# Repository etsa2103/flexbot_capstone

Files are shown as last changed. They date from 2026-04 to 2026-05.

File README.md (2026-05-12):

# FlexBot Reverse Engineering and ROS Integration

## Overview

The goal of this capstone project was to repurpose the FlexBot so that it can serve as a general mobile platform for future robotics research and teaching projects at Penn. The FlexBot is a differential drive industrial robot donated to GRASP by Berkshire Grey.  

The repurposing process included documenting the robot’s hardware and electrical architecture, evaluating its custom control software, removing application-specific hardware, and integrating new systems including a LiDAR, external computer, and odometry pipeline. The completed system was integrated into ROS 2 to support teleoperation, odometry, and SLAM while also producing documentation for future users and development.

<p align="center">
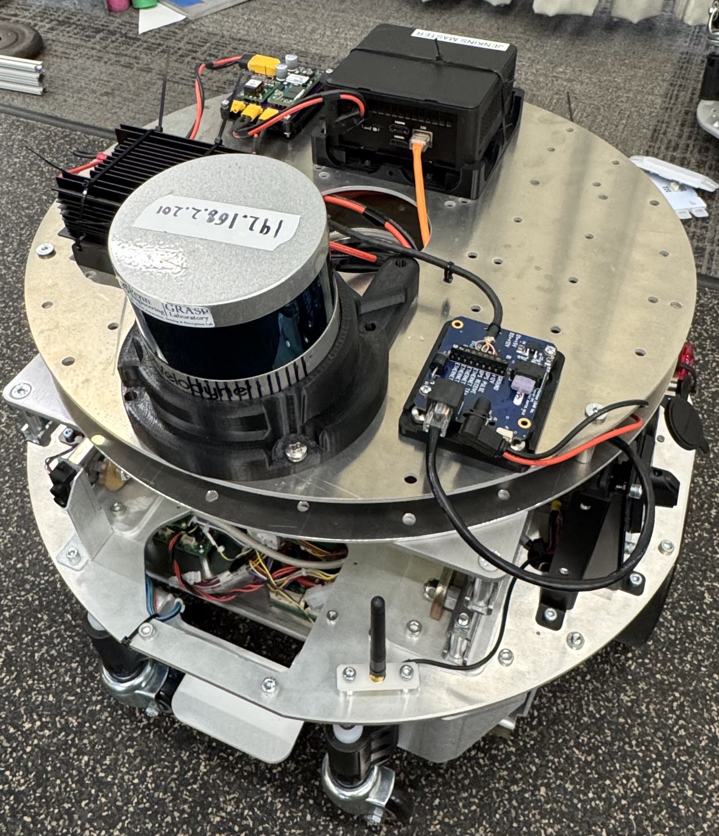
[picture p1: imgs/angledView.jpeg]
  
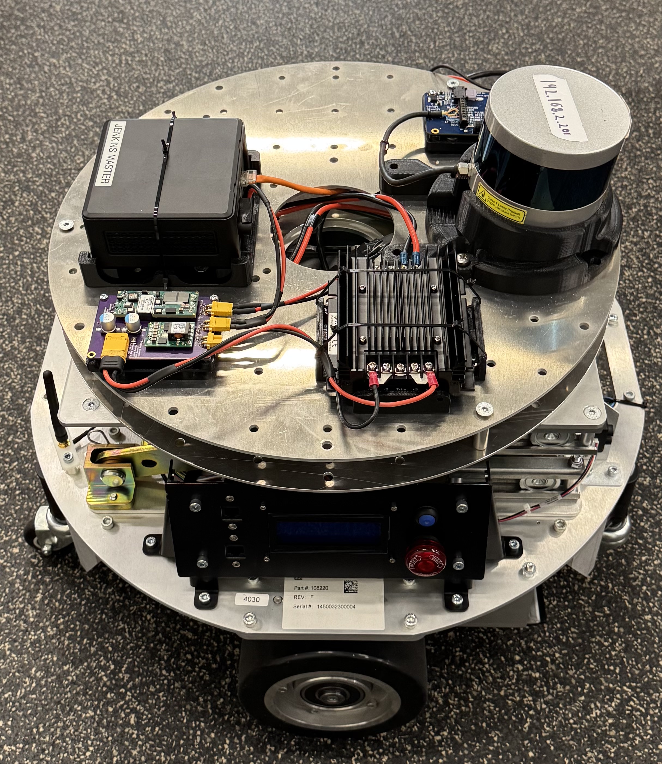
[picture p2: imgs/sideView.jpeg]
  
</p>

---

## Hardware

The robot hardware can be separated into three main components: the Mobile Base, the Scissor Lift Stage, and the Rotary Stage. Below is a brief description of each subsystem, while the full hardware documentation can be found on this [Miro Board](https://miro.com/app/board/uXjVJ2xI5w8=/).

### Mobile Base

The mobile base is the primary working platform of the robot and contains most of the core systems. Two drive motors provide mobility, while the onboard electronics manage power distribution, sensing, and computation. The base includes components such as the Motor Control Boards (MCBs), Power Distribution Board (PDB), sensors, LEDs, WiFi antennas, and the Application Processor Board (APB). These systems work together to support autonomous operation, sensor processing, and communication with external systems.

### Scissor Lift Stage

The scissor lift stage sits above the mobile base and provides vertical movement through a motorized scissor lift mechanism. It also contains a cable routing channel that allows wiring to safely pass from the mobile base to the upper stage without becoming pinched during movement.

### Rotary Stage

The rotary stage was originally designed to allow the top section of the robot to rotate independently from the base using a dedicated rotary motor and platform assembly. This stage remains present on the original FlexBots donated to Penn, but for this project it was removed and the available power was redirected to support the external computer and LiDAR.

---

## Electrical Connections

The diagram below shows the overall electrical layout of the robot and the connections between the major PCBs and subsystems. Rather than labeling every individual wire within each cable, the diagram focuses on the primary connectors and subsystem relationships to provide a clearer system-level overview.

<p align="center">
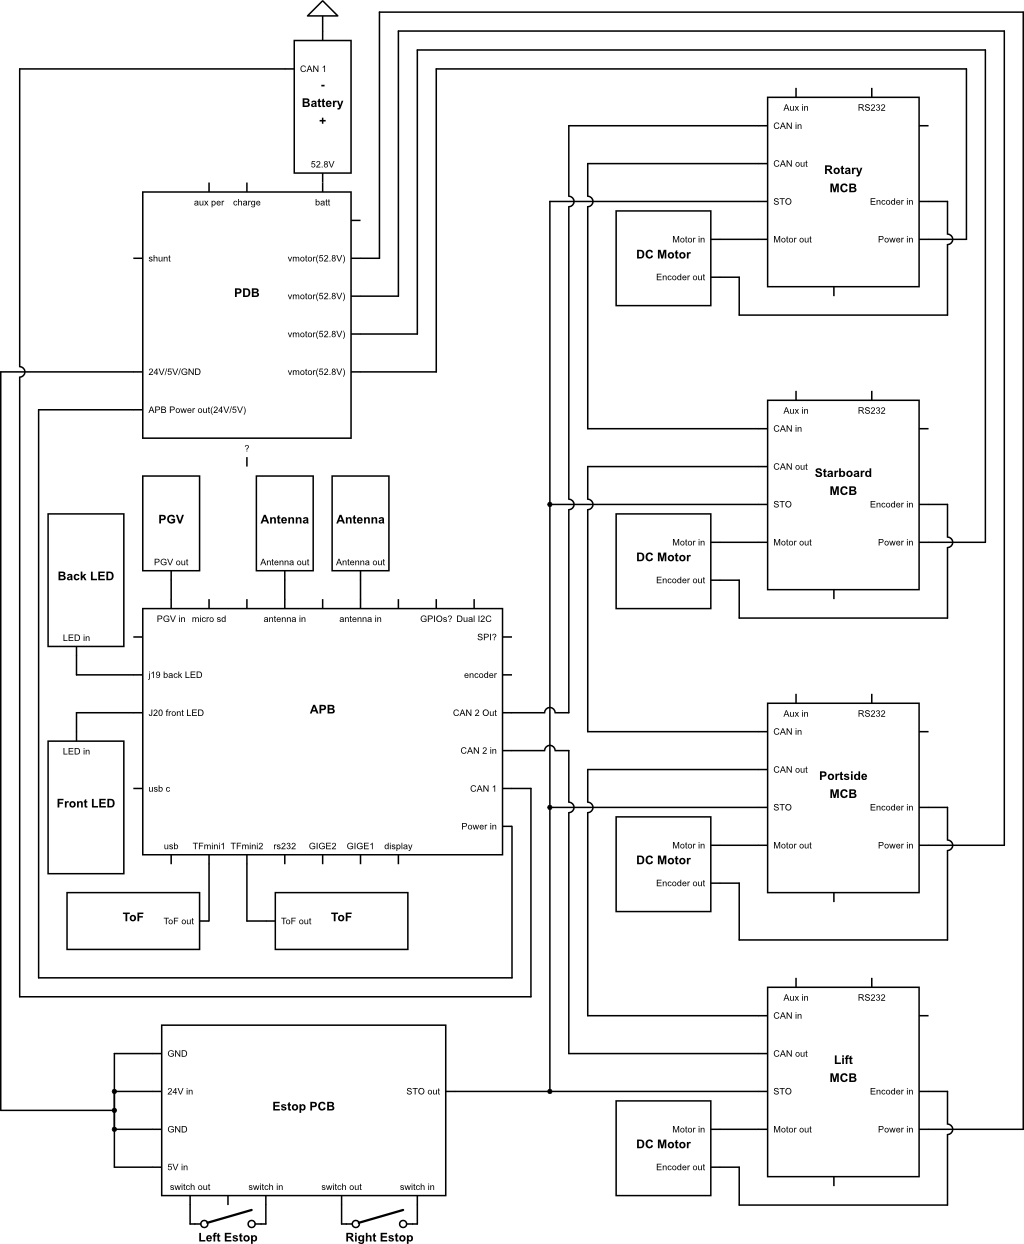
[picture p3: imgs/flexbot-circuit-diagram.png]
  
  <br>
  <font size="5"><b>Figure 1: Circuit Diagram of FlexBot Internal Electronics</b></font>
</p>

---

## Software Analysis

To gain control of the FlexBot’s internal systems, I first established direct serial communication with the onboard CPU. This allowed me to monitor the boot sequence and better understand the robot’s operating system environment. The CPU automatically attempted to connect to a WiFi network called `bg-flexbot-wifi6`, so I recreated the expected network environment in order to gain SSH access to the internal filesystem.

Reverse engineering the robot’s CAN network was necessary to gain control of the motors. With the help of Kartik Virmani from MOD Lab, CAN traffic was monitored while the robot’s built-in maintenance software executed known movement commands. By correlating CAN packets with specific robot actions, we identified the CAN IDs responsible for motor velocity commands and sensor data, ultimately allowing custom control scripts to bypass the original software stack.

All code developed for the low-level onboard computer can be found in [this branch](https://github.com/etsa2103/flexbot_capstone/tree/low_level_cpu) of the project repository. That branch also includes setup instructions and documentation for replicating the process.

---

## Modifications

Several hardware modifications were made to adapt the FlexBot for research applications and external hardware integration.

To bypass restrictions imposed by the proprietary safety board, the board was disconnected and 24V power was manually rerouted to the Safety Torque Off (STO) pins on the Motor Control Boards (MCBs). This 24V supply was sourced from the Power Distribution Board (PDB) and routed through both Emergency Stop (E-stop) buttons to preserve a functional hardware safety mechanism during operation.

In collaboration with Jaime Romero, the original rotary stage was removed and replaced with a custom top plate that provides a stable mounting surface for additional hardware. Custom 3D-printed mounts were also designed for the VLP-16 LiDAR, external high-level computer, and power distribution hardware. The CAD files for these mounts can be found [here](CAD). Power for the new hardware was sourced directly from the robot’s PDB and routed to the modified top assembly.

The resulting hardware architecture is shown below, while additional documentation can be found in the modified hardware section of the [Miro Board](https://miro.com/app/board/uXjVJ2xI5w8=/).

<p align="center">
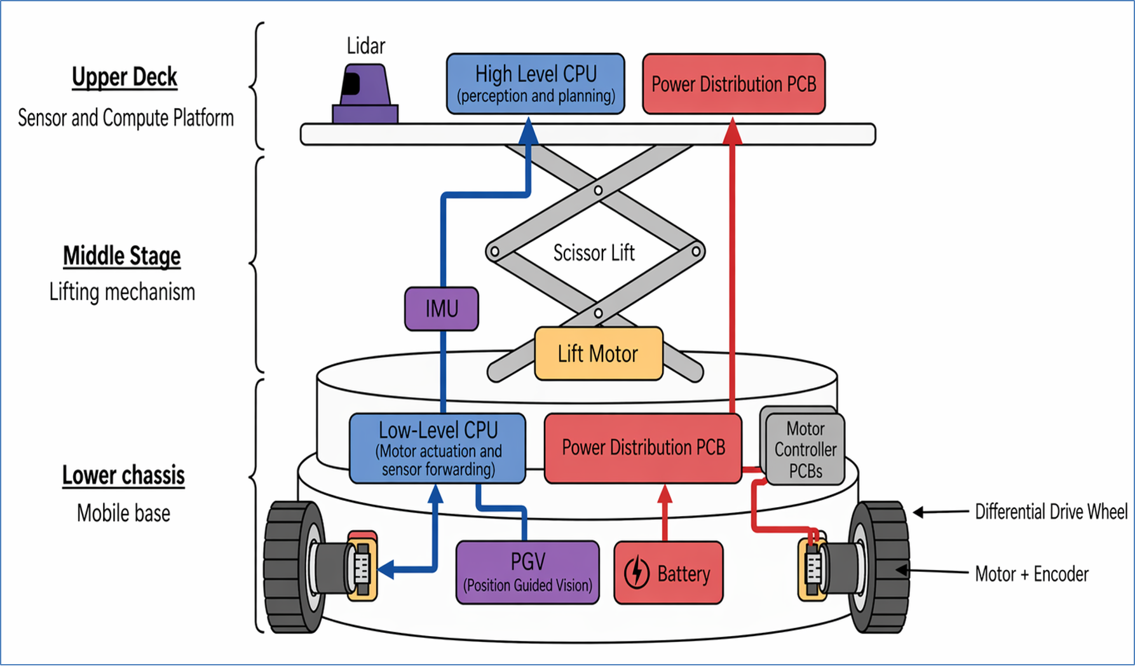
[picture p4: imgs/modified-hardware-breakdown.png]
  
  <br>
  <font size="5"><b>Figure 2: Hardware Breakdown of Modified FlexBot</b></font>
</p>

Because the original system relied on proprietary Berkshire Grey charging docks that were unavailable, an external charger was used to safely recharge the batteries.

---

## ROS Integration

To integrate the FlexBot into ROS 2, a dedicated Ethernet connection was established between the robot’s low-level embedded computer and the new external high-level computer. The low-level system processes raw hardware telemetry and continuously streams this data as UDP packets to the high-level computer. Custom ROS 2 nodes running on the high-level system capture the UDP data and publish it to standard ROS topics.

This architecture supports teleoperation, wheel odometry, and 2D SLAM using the integrated VLP-16 LiDAR. The overall software structure is summarized in the figure below.

<p align="center">
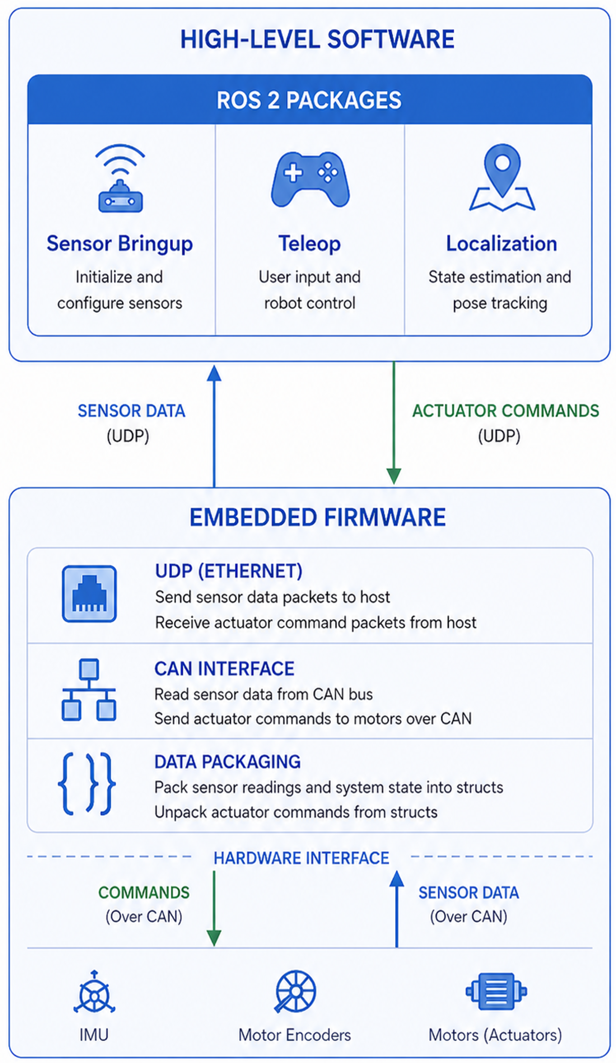
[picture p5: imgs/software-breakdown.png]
  
  <br>
  <font size="5"><b>Figure 3: Software Breakdown of Modified FlexBot</b></font>
</p>

Operational data, including maps, sensor feeds, and hardware telemetry, is visualized through a custom Foxglove Studio dashboard shown below.

<p align="center">
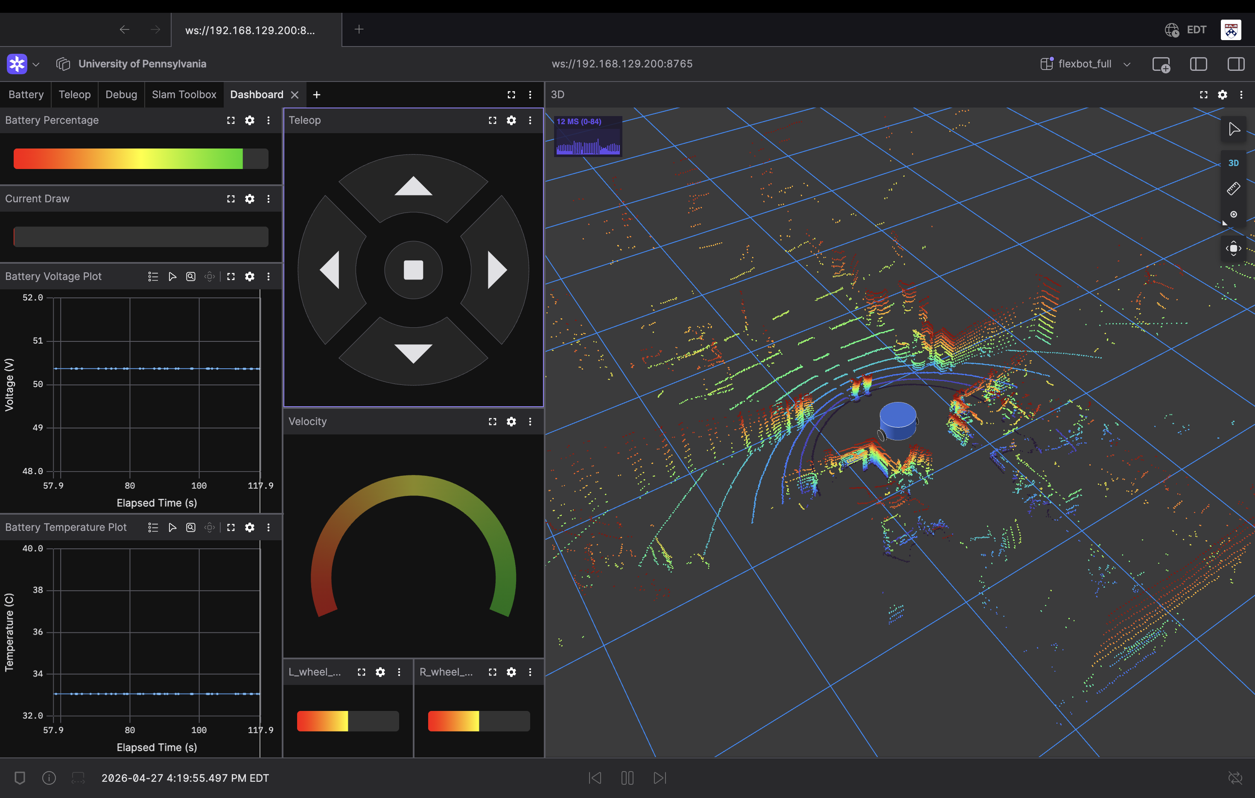
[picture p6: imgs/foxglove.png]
  
  <br>
  <font size="5"><b>Figure 4: Foxglove Visualizer</b></font>
</p>

All code developed for the high-level computer can be found in [this branch](https://github.com/etsa2103/flexbot_capstone/tree/high_level_cpu) of the repository. That branch also contains setup instructions and documentation for replicating the system.

---

## Side Notes and Next Steps

There are several remaining limitations and opportunities for future improvements to the FlexBot platform. When charging the robot, the main power switch must remain on or the batteries will not charge properly.

While the mobile base and LiDAR systems are fully operational, the scissor lift stage, LEDs, LCD display, PGV, and time-of-flight sensors are not yet fully integrated into ROS. The `low_level_cpu` branch contains several scripts that attempt to access these systems, but they are not currently exposed through ROS nodes running on the high-level computer.

Future development goals include integrating a 3D SLAM pipeline to better utilize the VLP-16 LiDAR, followed by obstacle avoidance and autonomous exploration or mapping behaviors for more advanced autonomous operation. Additional documentation collected throughout the project can be found in [this folder](additional_docs) of the repository.

---

## Acknowledgment

**Advisors:** I would like to thank Fernando Cladera and Dr. M. Ani Hsieh for their consistent advice and support throughout this project.

**Technical Contributors:** I would like to recognize Jaime Romero for his CAD designs and debugging assistance throughout the project. I would also like to recognize Kartik Virmani for his contributions to the reverse engineering and software development work included in this repository.

**Institutional Support:** Special thanks to Berkshire Grey for donating 30 FlexBot platforms to GRASP for research and educational use.

**Cornell University:** Thanks to Chris Bauer for providing documentation and insights from previous work on the robot platform.

## Appendix

- Kartik’s Github  
  https://github.com/virmani11kartik/bg_bot

- Kumar Robotics Github  
  https://github.com/KumarRobotics/kr_flexbot

- Miro Hardware Documentation  
  https://miro.com/app/board/uXjVJ2xI5w8=/

- Circuit diagram  
  https://www.circuitlab.com/circuit/pdmw4kpy644g/flexbot-circuit-diagram/

- Slack  
  https://app.slack.com/client/T09S1APBSHY/D09S4T6TL04

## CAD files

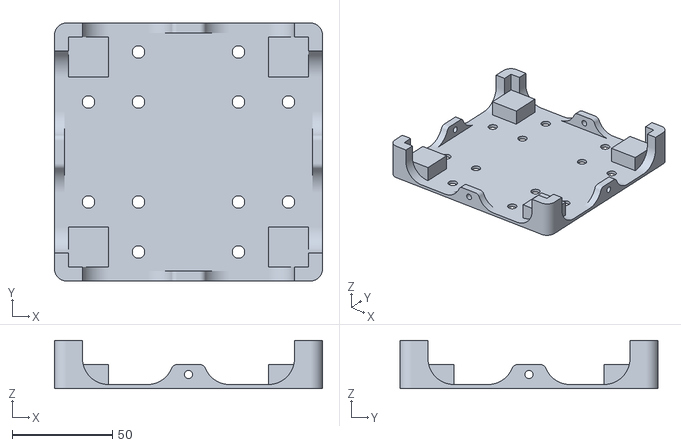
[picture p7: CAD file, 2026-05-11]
CAD/computer_mount.stl
134.0 x 129.0 x 24.0

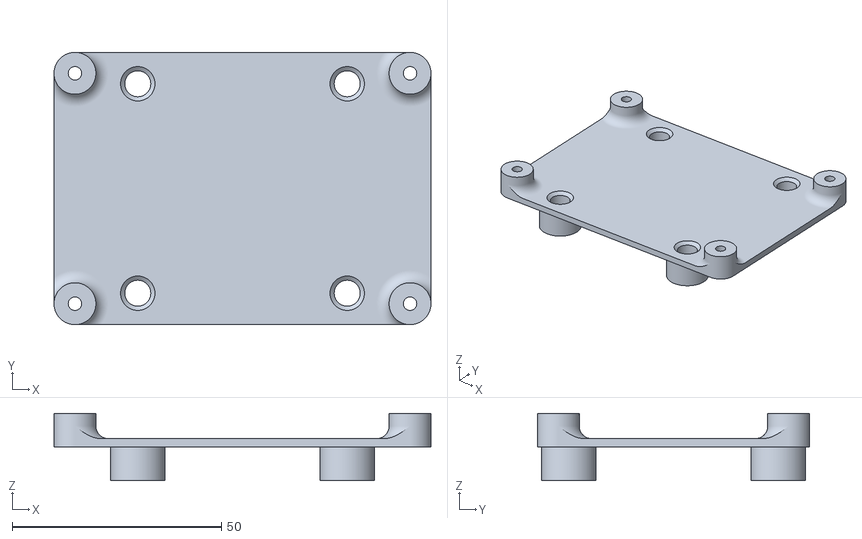
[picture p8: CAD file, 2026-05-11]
CAD/voltage_converter_stand.stl
90.0 x 65.0 x 16.0

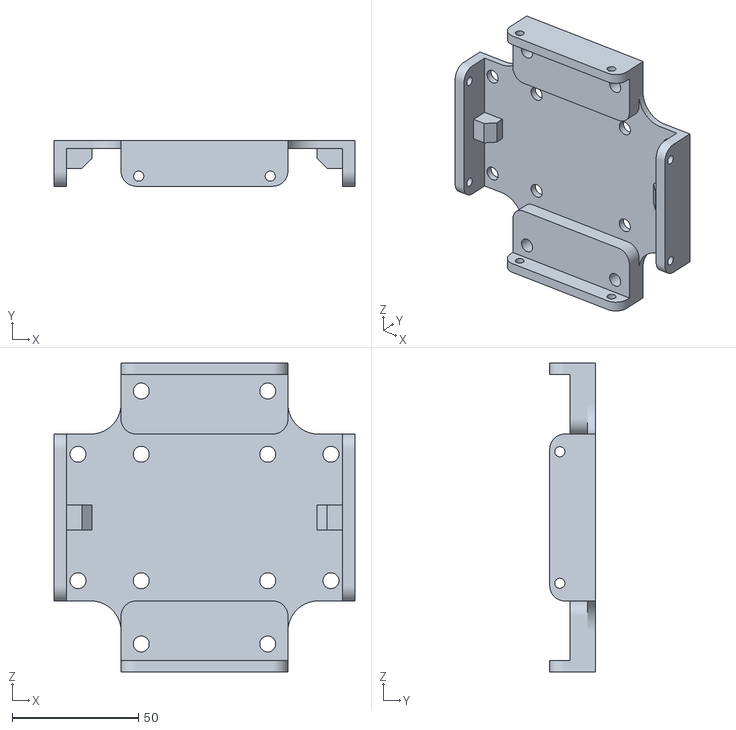
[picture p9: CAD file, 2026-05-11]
CAD/voltage_regulator_stand.stl
119.0 x 18.0 x 122.0

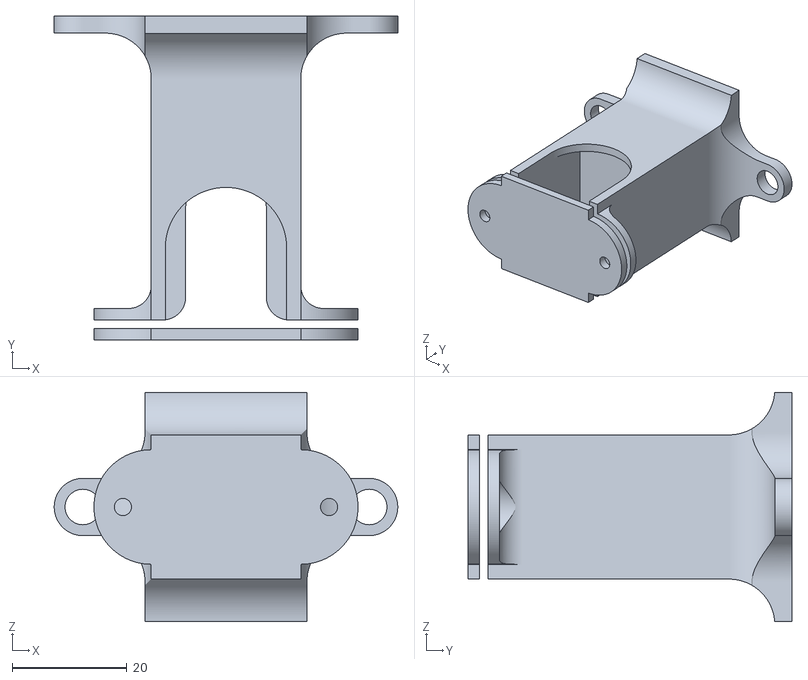
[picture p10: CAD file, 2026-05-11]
CAD/flir_camera_stand.stl
60.0 x 56.6 x 40.0

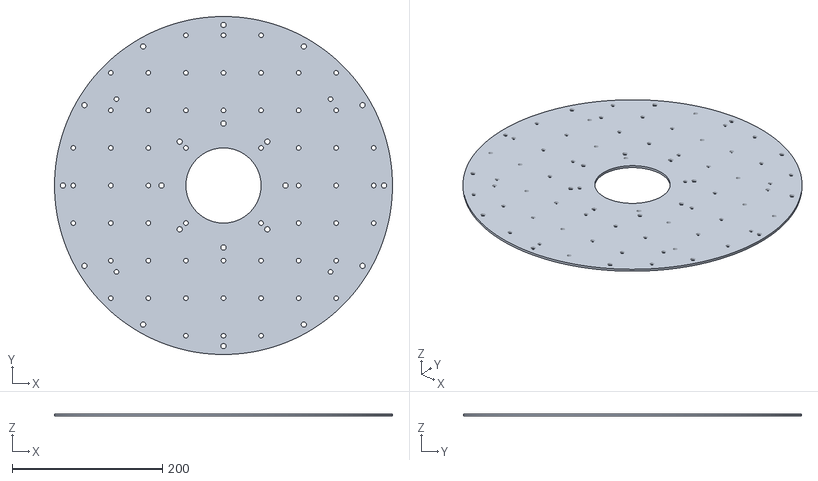
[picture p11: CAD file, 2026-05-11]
CAD/top_plate.stl
450.0 x 450.0 x 3.00

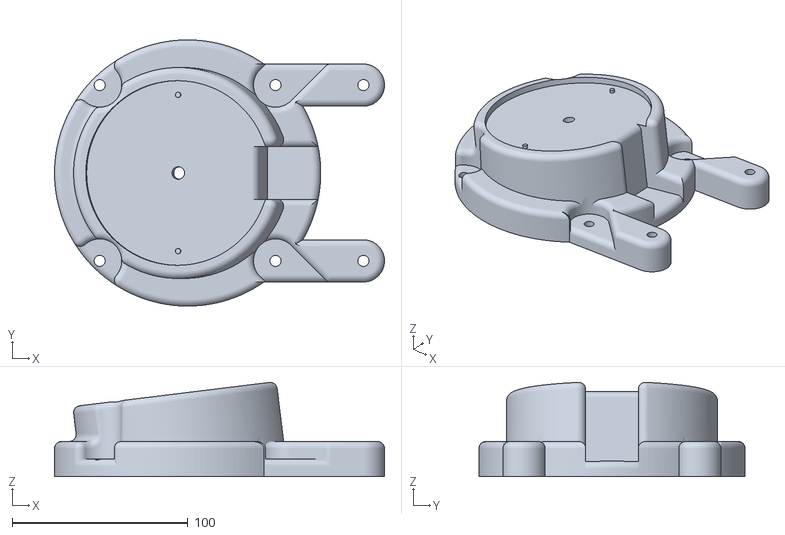
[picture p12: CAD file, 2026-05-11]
CAD/VLP16_mount.stl
187.7 x 151.5 x 53.6

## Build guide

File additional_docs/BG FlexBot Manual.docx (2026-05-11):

FlexBot Manual

FlexBot Theory of Operation Document Revision History

Revision | Date | Brief description of the Changes | Section(s) affected | Originator of Change
01 | 04/22/2022 | Initial Release | | Paul Conroy

The information in this document is current as the of the date of publication and is subject to change without notice.

Table of Contents

# Table of Figures

# FlexBot Overview

The FlexBot (PN: 108220) is the mobile robot that is a major component of the FlexTiles system. It is responsible for the movement and physical sortation of containers. It picks up containers from the induct FlexFeed, drives the container to the FlexShelves for temporary storage, and then drives it to the discharge FlexFeed. The FlexBot is capable of forward, limited backward, and rotation motion while the payload deck is capable of lift, lower, and rotation. Additionally, the FlexBot also has additional built in safety features to ensure safe operations.

The FlexBot has a fixed orientation described as port and starboard; standardizing orientation terminology to reduce chances of confusion. The port side of the FlexBot has the power switch while the starboard side of the FlexBot has the LCD. See below for pictures of the port and starboard sides of the FlexBot.

In this chapter, the part number for the illustrated item is displayed within the parentheses as shown in Figure 1.

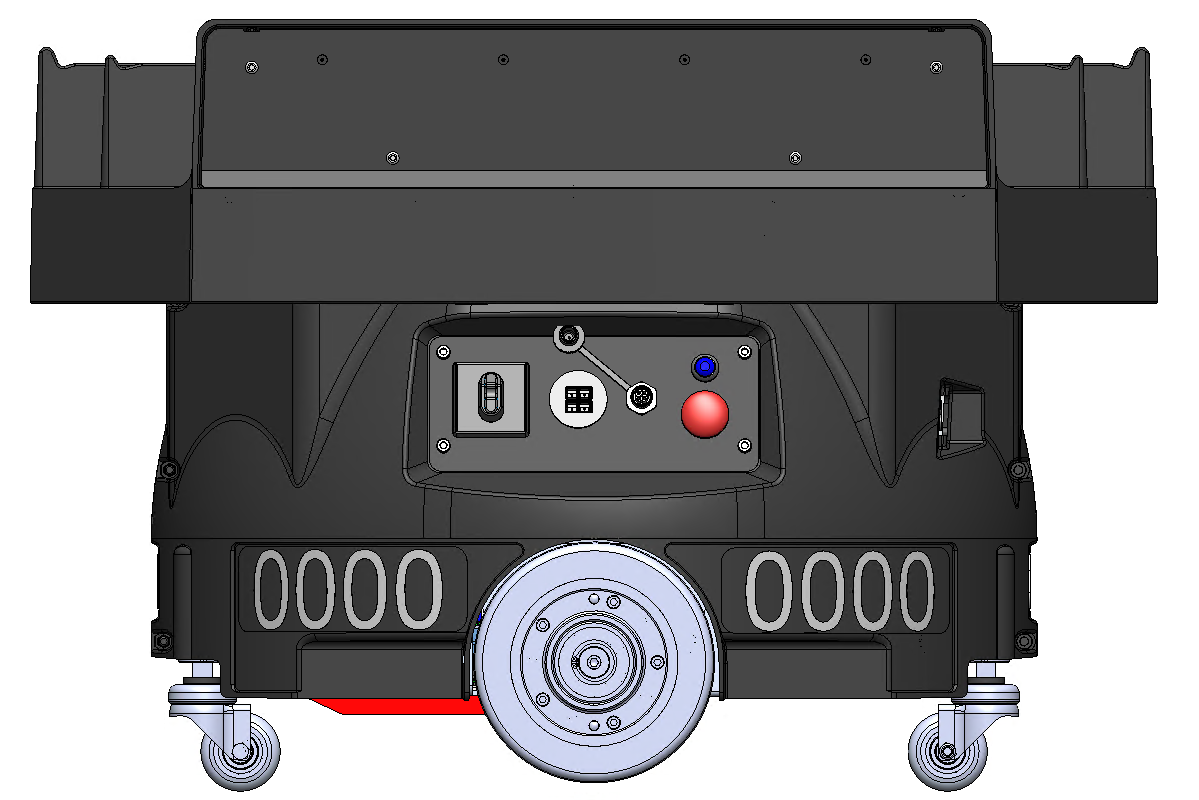
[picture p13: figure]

Figure 1 - Port Side of FlexBot

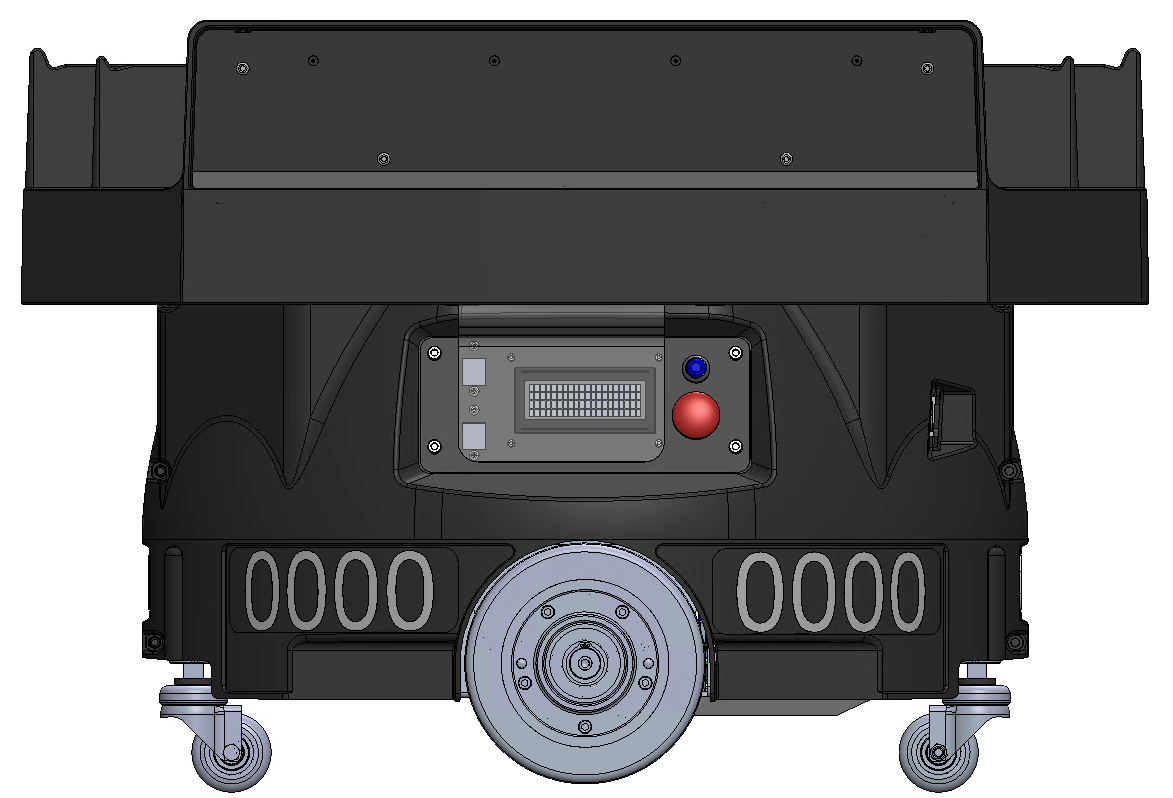
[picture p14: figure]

Figure 2 - Starboard Side of FlexBot

# Major Sections of the FlexBot

Section | Contains
Mobile Base | Contains the drive wheels and motors, the battery, the majority of the PCBAs
Payload Lift and Lower | Lifts and lowers the payload deck. It connects the drive base to the rotary stage.
Rotary Stage | Rotates the payload deck.
Payload Deck | The large plastic piece on top of the FlexBot that holds the containers as they move. There are four pairs of sensors used to detect whether there is a container on the payload deck.
FlexBot Housings and Covers | The outer pieces of plastic that cover the FlexBot.

## Mobile Base

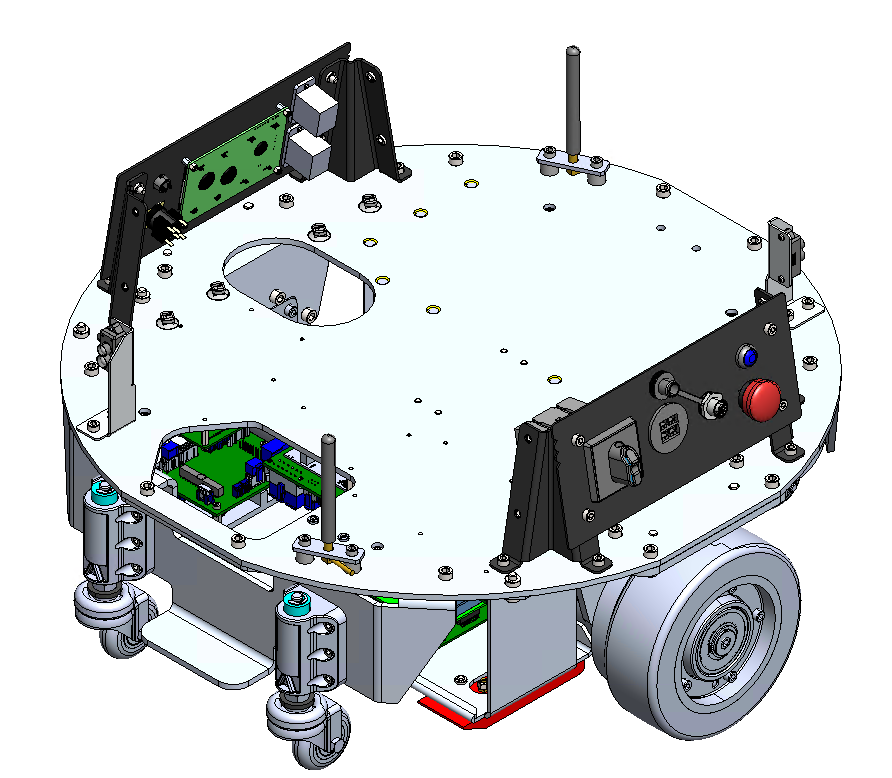
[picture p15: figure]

Figure 3 - Mobile Base: PN

The mobile base (PN: 107744) of the FlexBot is the core of the robot. It holds a large majority of components that are critical to the FlexBot’s function. Critical areas of the mobile base are listed below.

### Drive Motors

The drive motors (PN: 108471) are what allows the FlexBot to move in any direction. These motors can spin in both directions. FlexBots normal travel motions are forward and rotating either to the port or starboard. The port and starboard drive motors use the same part number.

Figure 4 - Drive Motors

### Battery

The FlexBot is powered by an onboard battery (PN: 109100). It requires periodic charging done automatically during normal operation and is managed by the FlexBot firmware. During maintenance and debugging the battery may have to be charged manually.

To access the battery you must remove, or swing open the caster bracket (PN: 108078) and then undo a Velcro strap that is holding the battery in place. Once the Velcro straps are undone, the battery can be partially slid out of the battery bay. Two final wired connections must be disconnected to free the battery from the FlexBot.

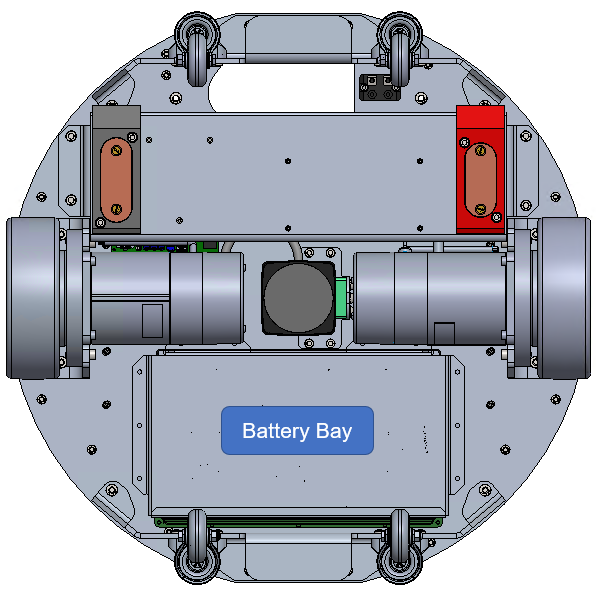
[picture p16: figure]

Figure 5 - Battery Bay Location

Figure 6 - Caster Bracket Location

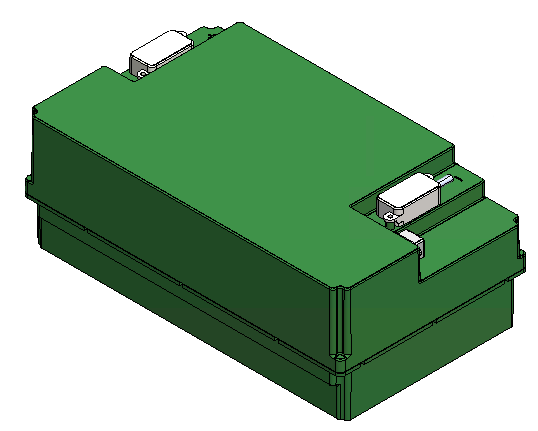
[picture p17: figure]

Figure 7 - Battery

### Battery Charging

The Charging & Electronics Bay ((PN: 109445) and contacts contain the electronic systems and pads for the FlexBot to charge the onboard battery using the charging points on the FlexTiles floor.

To reduce the risk of the charging system shorting, the negative contact is larger to ensure it connects first.

The positive charging contact block is colored red while the negative charging contact block is colored black.

Figure 8 - Charging and Electronics Bay

## User Interface (UI)

### Port Side UI

Figure 9 - Port Side

Part | Purpose
Power Switch | Physically controls the power state of the FlexBot. The power switch in the vertical position is off and in the horizontal position is on.
Emergency Stop | This red button inhibits any FlexBot motion when pressed. Rotate the button ¼ turn clockwise to release the button. There is an E-Stop button on both sides of the FlexBot. Both operate in the same manner. Only one needs to be engaged to stop motion. This button will blink twice per second when engaged and no light will be on in normal operation.
Dongle Port | The maintenance dongle plugs in this port when performing maintenance and debugging on the FlexBot
Shore power Port | Used to charge the battery manually when the FlexBot is off the field during maintenance.
Safety Reset Button | This blue button is used to reset the safety system in the FlexBot. There is one on both sides of the FlexBot. The small LED in the center of this button will signify one of the three different states: - Off- Normal Operation - Blinking twice per second - The button needs to be pressed to enter a normal operating state - Blinking once every three seconds - The FlexBot is located outside of the normal operating zone.

### Starboard Side UI

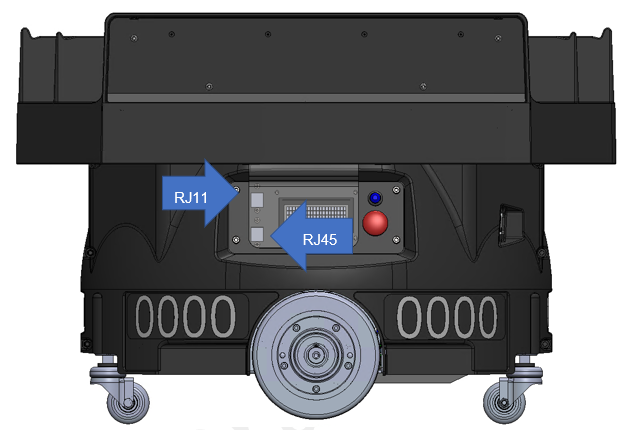
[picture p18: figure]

Figure 10 - Starboard Side

Part | Purpose
LCD Screen | Displays messages about errors, state of the FlexBot, FlexBot IP address, and other aspects of the FlexBot. The LCD will display relevant messages during maintenance steps.
Emergency Stop | This red button inhibits any FlexBot motion when pressed. Rotate the button ¼ turn clockwise to release the button. There is an E-Stop button on both sides of the FlexBot. Both operate in the same manner. Only one needs to be engaged to stop motion.
RJ11 Port | This port is used during the manufacturing process and is not active once it leaves the manufacturer.
RJ45 Port | Wired communication port used for direct Ethernet connection to the FlexBot.
Safety Reset Button | This blue button is used to reset the safety system in the FlexBot. There is one on both sides of the FlexBot. The small LED in the center of this button will signify one of the three different states: - Off- Normal Operation - Blinking twice per second - The button needs to be pressed to enter a normal operating state - Blinking once every three seconds - The FlexBot is located outside of the normal operating zone.

## Casters

The four casters (PN: 114307), two on the front and two on the rear, provide independent suspension for the FlexBot.

Figure 11 - Casters

## PGV (Position Guided Vision)

The PGV (PN: 108171) scans the fiducials. The PGV is a core component to determining the drive path and FlexBot behavior; using information gathered from scanning each fiducial such as angle of attack, and time between fiducials.

The PGV is connected to the APB (application processor board) using a physical cable. The APB processes the information from the PGV and sends the appropriate commands to other components of the FlexBot, such as drive motors.

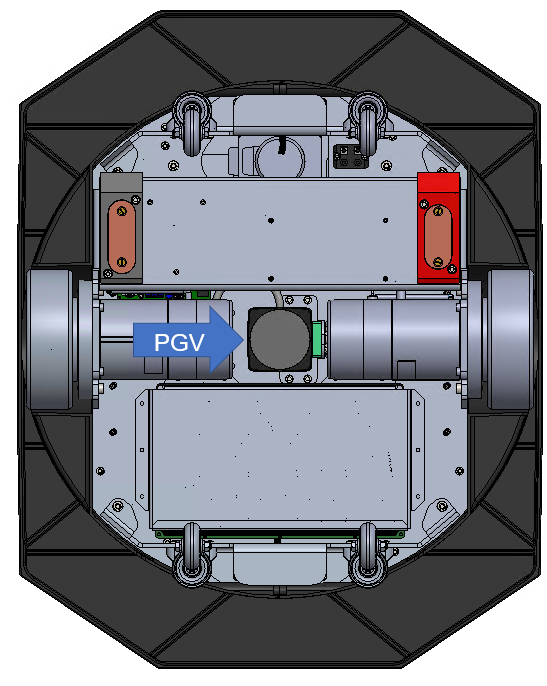
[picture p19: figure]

Figure 12 – PGV location

## PCBAs and cabling

### Motor Control Board (MCB)

- Controls the drive motors
- QTY-2

### Application Processor Board (APB)

- Runs most of the logic for the FlexBot and sends control commands to other FlexBot systems. Major components are the SOM (System On Module), IMU (Inertial Measurement Unit)
- QTY-1

### Power Distribution Board (PDB)

- Responsible for managing and distributing the power to all the components in the FlexBot
- QTY-1

### Siemens Carrier Board (SCB)

- Responsible for all safety controls logic, or the FlexBot safety PLC.
- QTY-1

## WIFI Antenna

There are 2 WIFI antennas on the front and rear of the FlexBot that are responsible for the wireless communication between the FlexBot and the rest of the system.

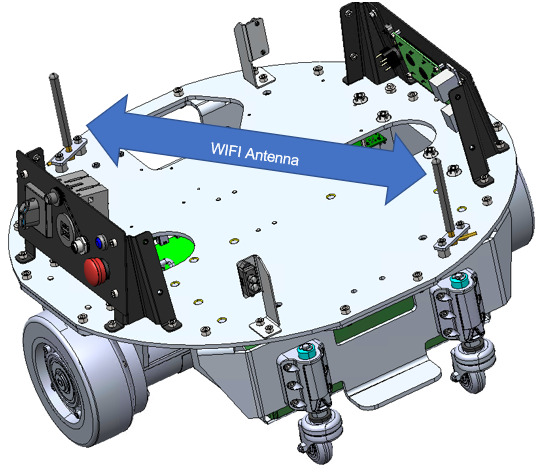
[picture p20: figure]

Figure 14 - WIFI antenna locations

# Payload Lift/Lower Assembly

The Payload Lift/Lower Assembly (108054) is what lifts containers off and onto the appropriate FlexFeeds and FlexShelves as the containers move through the robotic sortation system. The assembly is normally in the down position. It is only up when engaging or carrying a container. The up position is 100mm (4 in) above the down position.

The assembly uses a scissor lift to raise, lower and support the load using a motor controlled by an MCB.

The Payload Lift/Lower Assembly also connects the Mobile Base to the Rotary Stage, meaning that there are wires routed through this assembly. To avoid internal snags and to keep the motion areas clean, extensive wire and cable management is used on both local and pass-through wiring in and around the assembly.

The figure below illustrates the Payload Lift and Lower Assembly in the raised position without deck rotate assembly installed.

Figure 15 - Payload Lift and Lower Assembly

## Scissor Frame

The scissor frame is what supports the load and provides rigidity to the FlexBot while carrying a load. It is made up of two welded frames held together by cotter and clevis pins moving on rollers.

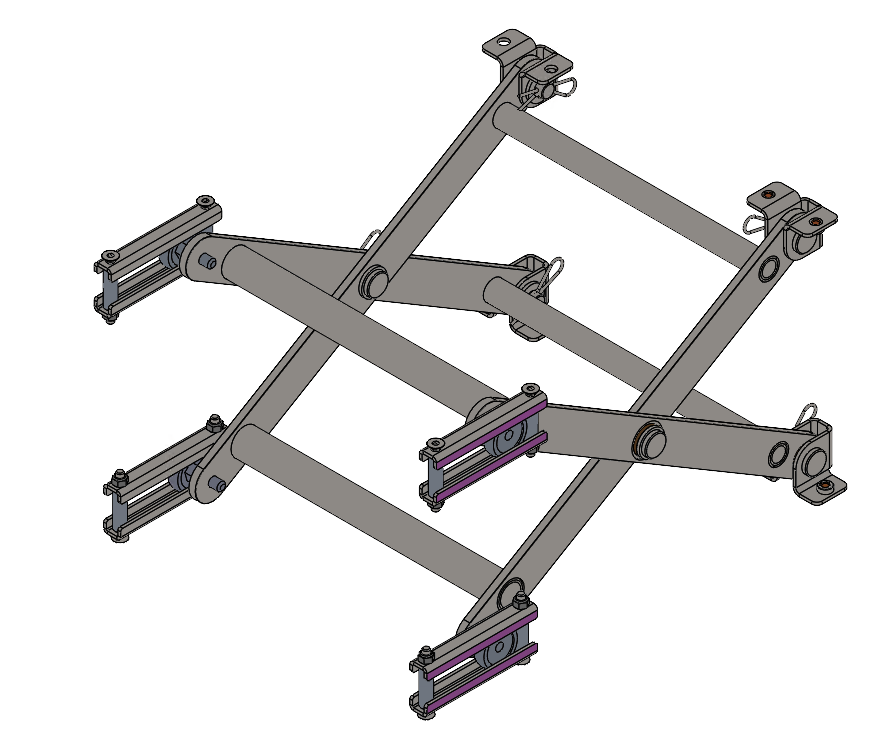
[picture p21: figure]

Figure 16 - Welded Scissor frame with rollers and pins

## Lift Motor/ Crank Arm/ Reed Switch

The lift motor, crank arm, and reed switch control the lift and lowering of the Payload Lift/Lower assembly.

The motor has a built-in encoder that helps it control its speed and position. The motor also has a gear box incorporated with it from the manufacturer. The gear reduction ratio of this motor is 100:1. It has a recommended torque of 34 N-m (300 lb-in). This motor is well guarded well within the FlexBot. During servicing the FlexBot it is recommended to follow safety procedures to avoid this motor becoming a pinch point.

The reed switch is a homing feature that tells the FlexBot when the deck is in the down position. A reed switch works using magnets, which means it is susceptible to fault when in close contact with other magnets.

The crank arm forms the connection between the motor and the payload.

Figure 17 - Motor, Crank Arm, and Reed Switch

Reed switch B

Motor

## Motor Control Board (MCB)

There are two MCBs mounted in the Payload Lift/Lower assembly, one for controlling the lift/lower motor and the other for controlling the deck rotate motor. These are also the same MCBs that are used to control the drive motors in the Mobile Base.

While these boards are physically identical, they have unique programming for the distinct functions that they perform. Due to this specialized programming, these MCB boards are not interchangeable.

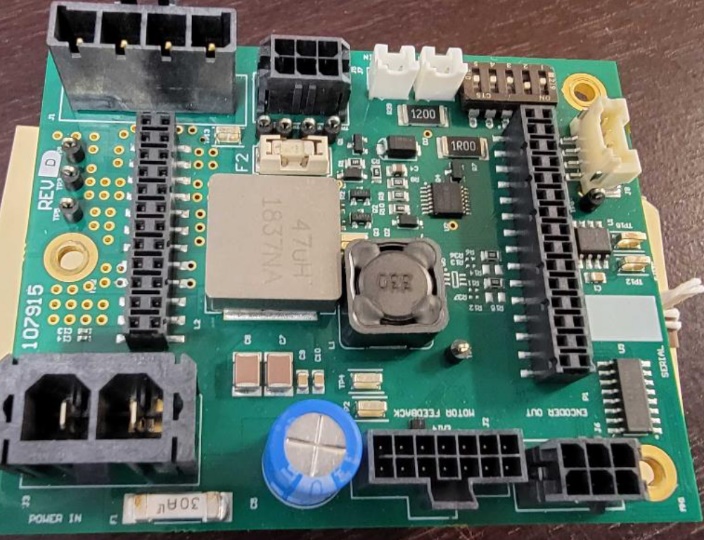
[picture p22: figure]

Figure 18 - Motor Control Board (MCB)

Figure 19 - MCB Locations on lift lower assembly

## Wire Routing & Cable Management

Wire routing and cable management is especially important in the Payload Lift/Lower assembly due to its range of motion. If wires and cables are not properly secured they may get caught and break. The cable management features are built in, and all should be used as designed.

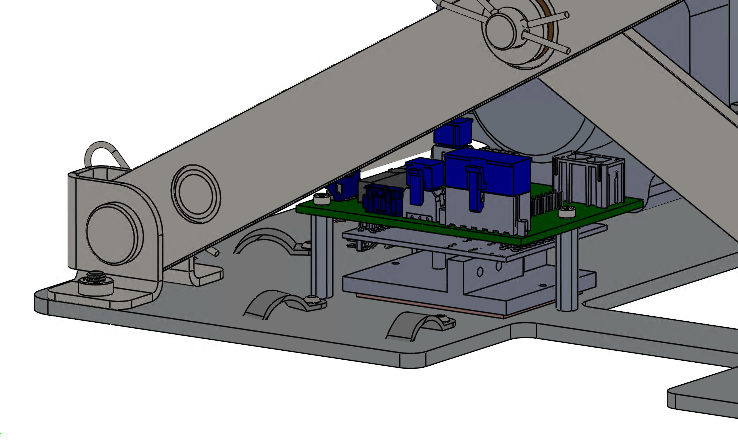
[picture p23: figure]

Figure 20 - Cable management locations - View 1

Figure 21 - Cable management locations - View 2

### Energy Chain Entrance Wires and Cables

These images show the energy chain entrance. The MCB Rotate Power cable (108174-04), Canbus cable (108180-04), Absolute Encoder cable (109825), Deck Presence Sensor cable (108183), and the STO cable (108187) are the cables routed within the energy chain.

The wires should be bundled together with zip ties and tied down with mechanical clamps at indicated locations to provide adequate clearance from the scissor lift frame. Tie wraps should not be used inside the energy chain track.

Mechanical tie down features, such as clamps, are provided to bundle cables and bind them such that they are clear of the scissor frame and do not move.

Cables must also be mechanically tied down to remain clear of the lift motor’s crank arm, especially the lift motor cables.

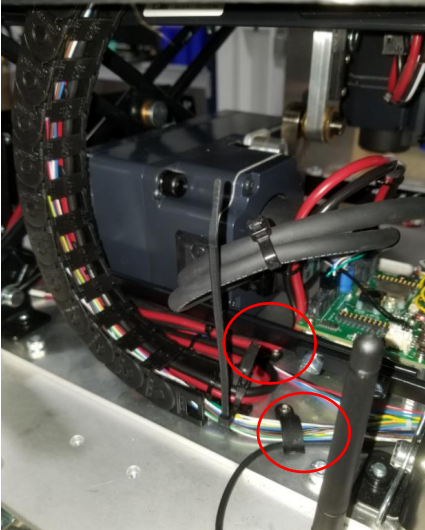
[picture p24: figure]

Figure 22 - Energy Chain Location Entrance

### Encoder and Slip Ring Wires and Cables

The Encoder and slip ring wires should be tucked out of the way using the wire clips, as shown below. It is important to ensure the cotter pin does not get entangled in these wires. This clevis pin is free to rotate and if wires are not secured properly, they may get caught on the cotter pin during normal operation.

Figure 23 - Encoder and slip ring wires

# Rotary Stage

The rotary stage is the assembly that rotates the payload deck. It can rotate infinitely due to design. The primary components are a motor that drives the rotation motion, a Motor Control Board that controls the motor, the drive mechanism that transfers the motion of the motor to the payload deck, a cover for safety, and a slip ring with an absolute encoder that controls the position while providing an electrical connection from the lower part of the FlexBot to the Deck Presence Sensors.

During normal operation, the deck normally orients in line with the shelves, while the mobile base drives and turns in different directions. The only time this is not true is when the FlexBot is discharging its container.

This assembly mounts directly to the top of the Payload Lift/Lower assembly as shown in Figure 24, and then payload deck mounts to the top of the deck rotate assembly.

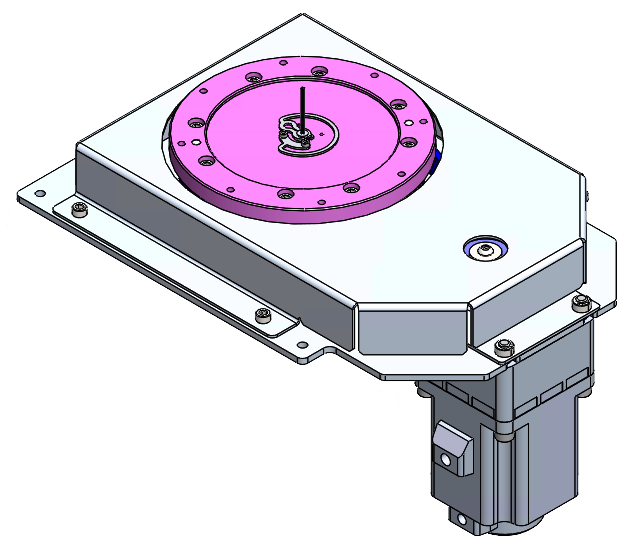
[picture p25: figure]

Figure 24 - Deck Rotate Assembly

## Deck Rotate Motor

The Deck Rotate Motor drives the rotation of the deck rotate assembly. There is a built-in encoder in the motor that helps control the motion and speed of the motor. A pulley installed on the motor shaft transfers the motion created by the motor to other parts of the system.

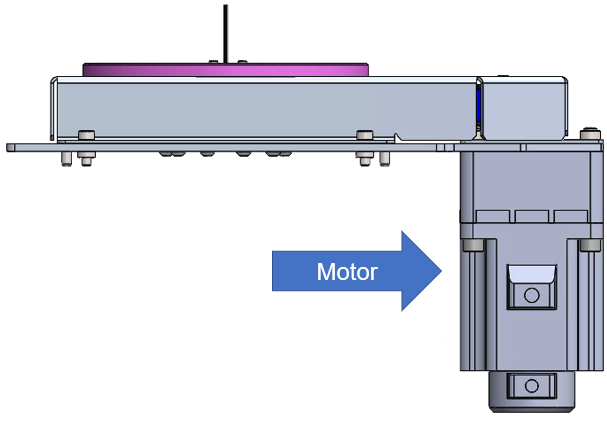
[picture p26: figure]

Figure 25 - Deck Rotate Motor

## Deck Rotate Motor Control Board (MCB)

The deck rotate MCB is mounted in the Payload Lift/ Lower assembly, seen in Figure 19. This MCB is almost identical to the other MCBs but is programmed to be used specifically for the deck rotate motor. The MCBs are not interchangeable.

## Pulley/Belt/Slew Ring

The pulley, belt, and slew ring transfers the motion from the deck rotate motor to the payload deck. The pully and slew ring are geared for a specific gear ratio and uses a specific tooth profile for the belt to ensure correct timing.

When disassembling and reassembling this assembly, there is no specific orientation that the pulley, slew ring and belt must be in. During maintenance, there is a process for re-zeroing this assembly which is done electronically. The pulley is keyed to allow a solid connection to the motor shaft.

Figure 26 - Pulley, Belt, and Slew Ring

## Cover Plate

The cover plate (108028) protects both the FlexBot and a person performing maintenance on the FlexBot. It is a sheet metal cover that is used to shroud the moving parts of the deck rotate assembly.

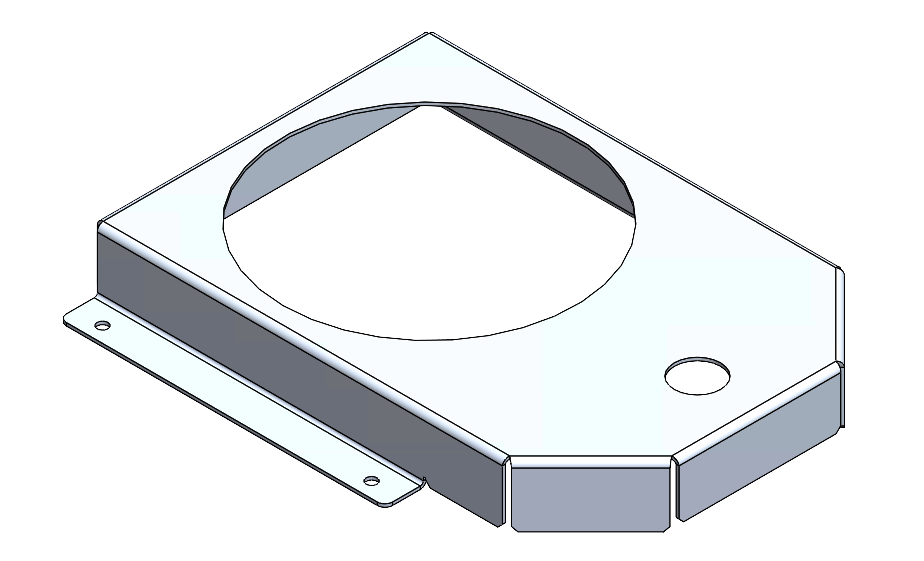
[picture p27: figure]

Figure 27 - Cover Plate, Belt Drive

## Slip Ring/Absolute Encoder

The slip ring and absolute Encoder (100204) are two separate components built into one assembly. The slip ring transmits electricity from the Mobile Base to the deck presence sensors while allowing for continuous and infinite rotational motion of the deck. The absolute encoder provides the rotational position of the deck to the FlexBot. These two components are assembled together and should be considered a single component.

Figure 28 - Slip Ring and Absolute Encoder - View 1

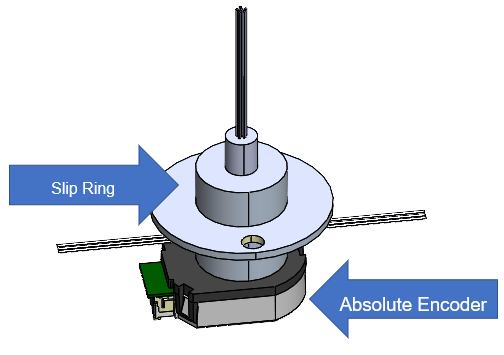
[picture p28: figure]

Figure 29 - Slip Ring and Absolute Encoder - View 2

## G-Clip

The G-clip (100204) connects the movement of the slew ring to the slip ring shaft. This connection allows the FlexBot to know the true position of the deck. It is made from spring steel and allows for limited eccentricity and compliance during rotation. During removal and install of the G-clip, it is important not to apply too much force and permanently deform the clip.

Figure 30 - G-Clip

# Payload Deck and Covers

## Molded Payload Deck

The molded deck (108817) physically contacts the payload on the FlexBot during handling. It is specially designed to interact with the FlexFeeds and shelves. There are a series of deck presence sensors either side of the deck facing inwards to detect whether there is a container on top or not.

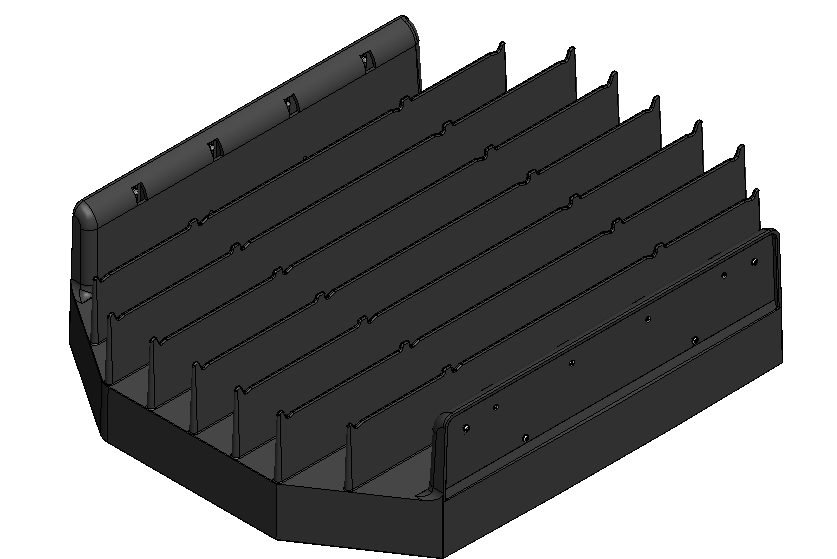
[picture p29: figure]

Figure 31 - Molded Deck with Side Covers

## Deck Presence Sensors

The Deck Presence sensors tell the FlexBot if there a container on the payload deck or not. They work by generating infrared light beams from transmitters on one side of the deck to receivers on the other side of the deck. Breaking the infrared light beams will signal the FlexBot that there is indeed an object on the deck.

Figure 32 -Deck Presence Locations

## Payload Deck Wire Guarding

There are two guards on the underside of the payload deck to protect the deck presence sensors wires.

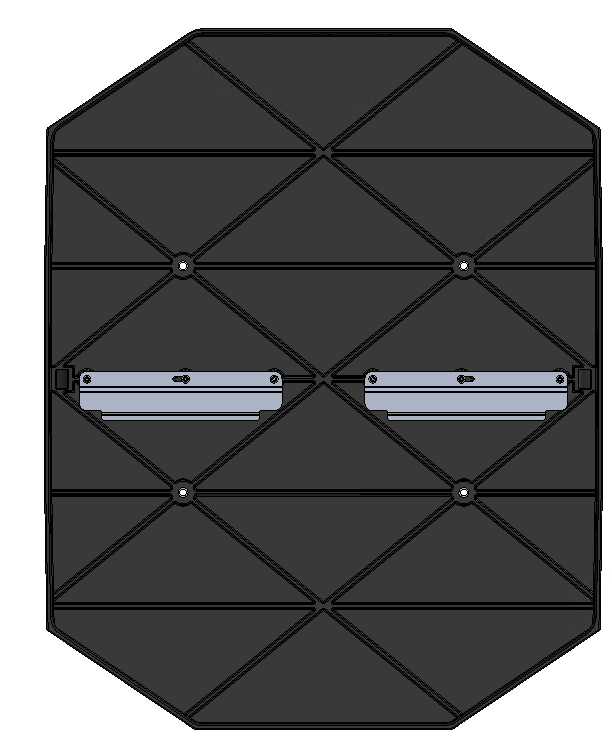
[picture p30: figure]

Figure 33 - Molded Deck with wire guards

## Housings and Shield

The housings and shields are used to minimize ingress of foreign objects into the FlexBot as well as protecting maintenance personnel. The housings covering the chassis and lower portions of the payload lift/lower assembly are identical parts on the port and starboard side. The upper portion of the payload lift/lower assembly is enclosed using another shield part.

Figure 34 - Housings and Shield

## LED Panels

Illuminating in assorted colors the LED Panel on the front and rear of the FlexBot indicates the state of the FlexBot. Below are descriptions of what the LED panel is indicating.

LED Color | Meaning
Green | Normal operation no container
Blue | Normal operation w/ container
Cyan | Charging
Purple | No connection to FlexBot manager
Flashing Yellow | Maintenance Dongle Inserted
Orange | No fiducial seen
Red | Safety stop (global E-Stop/pressing the E-Stop button)
Flashing Red | Safety System is not updating

# FlexBot Safety

## Safety Features during Operation

The FlexBot 2.0 has a safety system that is designed to have a supervisor roll in movement and location of the FlexBot as it moves on the FlexTile field.

The Safety System uses checks and balances to sense, validate and confirm the FlexBot is moving in an enabled FlexTile field zone.

Conversely, if a FlexBot is in a disabled FlexTile field zone, the supervisor component inhibits the FlexBot movement. There are two components of the system:

1. The FlexBot safety controller.

2. The High-Level Safety Controller.

The two devices communicate with each other validating location and ability to move in a FlexTile field zone. Both the FlexBot safety controller and High-Level Safety Controller use independent checks and balances to sense, validate and confirm the FlexBot’s location and the ability to move in an enabled FlexField zone.

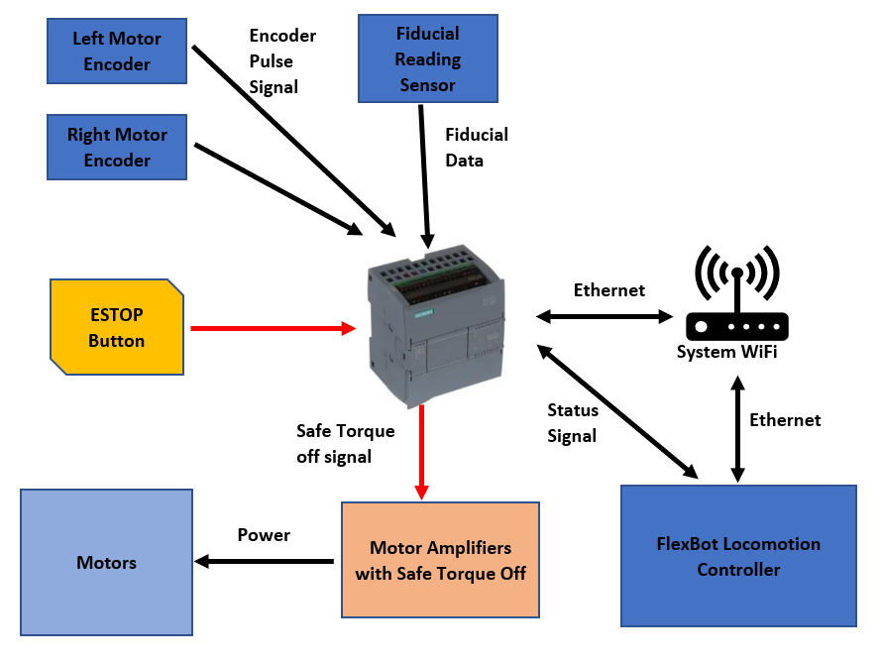
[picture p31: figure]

Figure 35 - FlexBot 2.0 Safety System Block Diagram

## Safety Controller Communication

The FlexBot Safety Controller and the High-Level Safety Controller exchange information 10 times every second. The High-Level Safety Controller only responds to verified information it receives from the FlexBot Safety Controller. The messages are communicated using a Siemens Profisafe protocol over Wireless Ethernet.

The Wireless Ethernet is an unsecured channel that is not safety rated nor 100% reliable. Safety systems can use such non-reliable communication because the devices at each end of the unsecured channel are safety devices that can make safety decisions in the absence of active communication.

The High-Level Safety Controller activates only a few tiles ahead of the FlexBot while leaving active a few tiles behind the FlexBot. As the FlexBot moves through the field tiles are activated in front of the FlexBot in the intended direction of the bot. If the FlexBot runs out of active tiles before the High-Level Safety controller activates new tiles the bot will stop.

The lack of a sequential response from the High-Level Safety Controller to the FlexBot Safety Controller is an indication of a shutdown condition.

Safety Controller Verification

As mentioned earlier, the FlexBot Safety System uses checks and balances to sense, validate and confirm the FlexBot is moving in an enabled FlexField zone.

The check and balances are outlined in the following individual validations. If any of the validations fail, the FlexBot Safety System informs the FlexBot controller of a pending shutdown process and movement stop.

Direction and distance measurements between fiducials

The FlexBot Safety Controller measures the distance traveled using the two encoder sensors on the two FlexBot locomotion motors.

Each encoder sensors produces two square wave signals that are changed into count and direction pulses that the FlexBot Safety controller keeps track of to measure the distance a FlexBot has moved. To validate that a FlexBot is moving in an expected manner, the calculated distance between scanned fiducials is verified with the expected distance between fiducials.

Correlation between distance travelled and new fiducials

As the FlexBot moves and measures distances, the FlexBot Safety Controller expects to see fiducials at known distances. The opportunities for fiducial data to be received are interpreted as windows of opportunity that open and close depending upon the distance traveled by the FlexBot.

If the FlexBot moves a distance equaling the distance between fiducials (within a degree of tolerance), a window of opportunity to receive a new fiducial opens and a new fiducial is expected. Conversely, if the FlexBot moves a distance less than the expected distance between fiducials, the window of opportunity to receive a new fiducial is closed and a new fiducial is not expected.

Further still, if the FlexBot has not moved from a fiducial, the window of opportunity to receive fiducial stays open expecting the same fiducial and a new fiducial is not expected. Only when scanning a new fiducial in an expected window of opportunity is a safety message with the new fiducial information sent to the Higher-Level Safety PLC to validate the fiducial.

Maximum velocity verification

In addition to The FlexBot Safety Controller measuring the distance traveled, the velocity of the FlexBot locomotion motors is also monitored not to exceed a maximum expected speed. As the controller on the FlexBot commands the locomotion motors to move, it reports the expected velocity to the FlexBot Safety Controller to verify that that locomotion motors are performing as expected. This validation indirectly verifies that the encoders are functioning as expected.

Siemens Profisafe message validity verification

The last validation check that the FlexBot Safety Controller performs is a validation of the Siemens Profisafe communication of the safety messages.

In the event of communication data corruption or loss, the communication values are set to fail safe values causing the FlexBot Safety Controller to perform a shutdown process and movement stop.

High Level Safety Controller Verification

Like the FlexBot Safety System, the High-Level Safety Controller also uses checks and balances to sense, validate and confirm the FlexBot is moving in an enabled FlexTile field zone.

The High-Level Safety Controller uses a separate set of checks and balances expanding validation diversity of the FlexBot Safety System. Those check and balances are outlined below in the following individual validations that are performed every time a safety message is received from the FlexBot Safety System.

Fixed map of fiducials of the FlexTile field

The High-Level Safety Controller has a fixed map of all the fiducials and their respective locations. When the FlexTile field is installed, a map is generated of all the fiducial locations and zones. The High-Level Safety Controller uses this map to validate the location and control the movement of the FlexBots on the FlexTile field.

FlexBots that are in enabled FlexTile zones are allowed to move freely while those FlexBots in disabled FlexTile zones are inhibited from moving.

Correlation of reported fiducials and a fixed map of fiducials
When a FlexBot sends a message about the fiducial seen to the High-Level Safety controller, that fiducial is checked to be on the fixed map of FlexTile field fiducial. Once a fiducial is validated, the FlexTile zone status is checked.

FlexBots that are in enabled FlexTile zones receive a reply from the High-Level Safety controller that the fiducial is validated and FlexTile field zone is enabled. FlexBots that are in disabled FlexTile zones receive a reply from the High-Level Safety controller that the fiducial is validated and FlexTile field zone is disabled.

FlexBot location history

In addition to validating the FlexBot reported fiducials are found on the fixed map, the High-Level Safety Controller also keeps a history of the last fiducial reported by a FlexBot. The last fiducial reported is validated to be adjacent to the current fiducial reported.

The fiducial history validation is to check if the fiducials reported are valid in sequence found in the fixed map as the FlexBot moves from one fiducial to another so the FlexBot cannot just report random fiducials any time.

Correlation of adjacent reported fiducials
The High-Level Safety Controller keeps a history of the last fiducial reported by a FlexBot. The last fiducial reported is validated to be adjacent to the current fiducial reported.

The adjacent fiducial validation checks if the fiducials reported are valid in sequence found in the fixed map as the FlexBot moves from one fiducial to another. This validation is so the FlexBot cannot just report random fiducials any time. As part of the Fiducial validation by the high-level safety system, one of the two fiducials that are adjacent to the currently reported fiducials must be equal to the fiducial last reported, or as in the history of the last fiducial reported. The system only validates two fiducials adjacent to the current reported fiducial thus allowing one fiducial to be missed and allow the current fiducial to be validated

### Fiducial Timeout

The FlexBot has the ability to miss a fiducial. There is a timeout of 4 seconds built into the FlexBot that if a fiducial is not seen it will stop driving and the LED will change from it’s current color to orange which means fiducial not sen.

Siemens Profisafe message validity verification

The last validation check that the High-Level Safety Controller performs is Siemens Profisafe communication safety message validation. In the event of communication data corruption or loss, communication values are set to fail safe values. Fail safe values cause the High-Level Safety Controller to send response messages to the FlexBot that the fiducial reported is invalid and the FlexBot must perform a safety stop.

Safety System User Interface

The FlexBot Safety System has a user interface consisting of an illuminated E-Stop and Reset button on the left and right side of the FlexBot. In addition, the maintenance connector is found on the left side of the FlexBot.

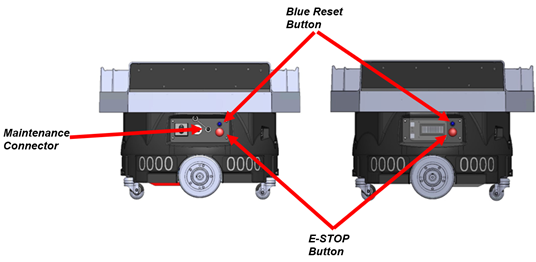
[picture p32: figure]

Figure 36 - FlexBot Safety System User Interface

### E-Stop Button

The red illuminated E-Stop button is a push Emergency Stop button that disables all the motors in the FlexBot from moving. The E-Stop button is pressed to activate the E-Stop and disable all motors of the FlexBot.

A “turn and pull motion” is required to deactivate the E-Stop. Following an E-Stop activation and deactivation, a reset procedure (see below) is required to re-enable the FlexBot motors.

### E-Stop Illumination

The E-Stop button has an illumination feature while the FlexBot is powered on. The E-Stop button is normally not illuminated when E-Stop is not activated, or the E-Stop button has not been pressed.

The illumination on both E-Stop buttons will flash twice per second after the button has been pressed to indicate that an E-Stop button has been pressed on either side of the FlexBot.

### Maintenance Connector

The FlexBot Safety System has a maintenance connector. A special maintenance dongle is connected to the maintenance connector putting the FlexBot Safety System into a maintenance mode disabling the fiducial validation.

While in maintenance mode, the FlexBot can be evaluated to ensure proper operations as a part of maintenance tasks. When the maintenance dongle is connected, a reset button (see below) must be pressed when indicated to enable the maintenance mode.

The Reset button must be pressed again, when indicated, when the maintenance dongle is removed to return the FlexBot to normal operation.

### Reset Button

The Reset button is a push button to set the FlexBot Safety System into a known operating state. The Reset button needs to be pressed when flashing to acknowledge and authorize the FlexBot Safety System to enter an operating state. This is the case after the FlexBot has recovered from an error or is powered on.

### Reset Button Illumination

The Reset button has an illumination feature while the FlexBot is powered on. The button illumination is normally off when the FlexBot does not need the attention from a technician.

The illumination will flash twice per second if the Reset button needs to be pressed by a technician to acknowledge and authorize the FlexBot Safety System to enter an operating state.

The illumination will flash once every three seconds when the FlexBot Safety System is inhibiting all motion on the FlexBot when the FlexBot is in a disabled FlexTile zone. This light pattern is only an indication the FlexBot is in a disabled zone and does not require any action by a maintenance technician.

## Maintenance Safety

Before a Robotics Technician (RT) performs maintenance on the FlexBot, and RT should be familiar with these concepts and processes to ensure a safe working environment.

### Safely Moving the FlexBot

The FlexBot is a 120-pound piece of equipment needing specials tools and multiple people to move it properly.

The recommended tool for moving the FlexBot while on the floor is the FlexBot Removal Tool (FRT). The FRT has a specially designed fork meant to interface with the casters of the FlexBot. The points of the tool insert under the metal flange of the caster when the handle is pushed down drive wheels of the FlexBot are lifted allowing easy movement of the FlexBot.

This tool should be used for manually moving/rolling the FlexBot on floors such as the FlexField, in the RSS Shop, and in between both areas.

Figure 37 - FlexBot Removal Tool (FRT) highlighting caster lift points

There are two ways for lifting the FlexBot: the FlexBot Lift and the Team Manual Lift. The FlexBot Lift is an electric lift. This lift has custom designed arms that clamps to the FlexBot. The lift is designed to be used for maintenance; the FlexBot must have the housings removed to safely clamp onto the FlexBot. The FlexBot lift can move the FlexBot up, down, and rotate it 360 degrees.

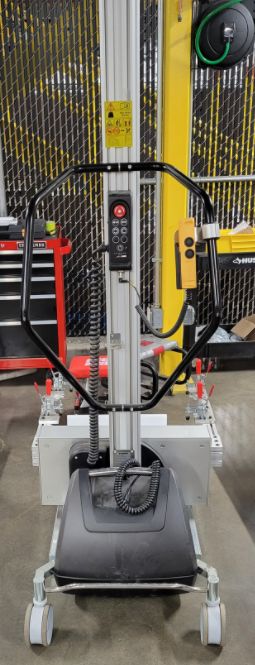
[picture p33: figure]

Figure 38 - FlexBot Lift

Figure 39 - FlexBot Lift Arms

The Team Manual Lift is a procedure requiring two people. This procedure is designed with the housings of the FlexBot still on. The housings of the FlexBot have hand holds designed into them for lifting it. This procedure is done when lifting the FlexBot onto to bench and onto the maintenance cradle.

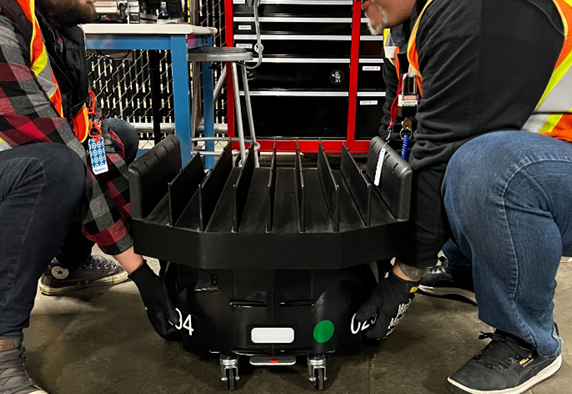
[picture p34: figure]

Figure 40 - FlexBot Team Lift

### Safely Performing Maintenance on the FlexBot

To safely perform maintenance on the FlexBot there are certain pieces of equipment and power states that you should be familiar with. There are two pieces of equipment recommended for working on the FlexBot: The FlexBot Lift and the FlexBot Maintenance Cradle. The FlexBot Maintenance cradle is designed to be used on a bench top. The FlexBot lift Is another maintenance tool like the cradle, but it allows a technician to easily work on the underside of the FlexBot.

The maintenance cradle elevates the FlexBot slightly off the bench so that the FlexBot can activate certain components freely and safely. The FlexBot should be placed on top of this fixture with the battery tray sitting inside section indicated below in the red box in the picture below. The electronics bay should sit inside the yellow box as shown in the picture below.

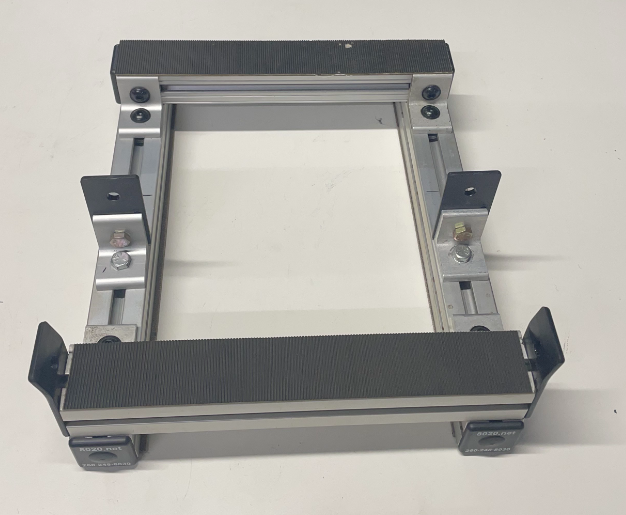
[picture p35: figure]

Figure 41 - The FlexBot Cradle Orientation

Once the FlexBot is held safely in one of these two pieces of equipment there are different power states it can be placed into depending on the type of maintenance being performed. The FlexBot can be placed into these various maintenance states via the port and starboard panels of the FlexBot.

Figure 42 - Port Side

Figure 43 - Starboard Side

Maintenance procedures can happen in these maintenance states:

1. Powered Off State - The FlexBot is put into this state by turning the power switch to the off position. When the FlexBot is powered off all the components no longer have power.

This powerless state allows for components to be serviced safety while ensuring technician safety as well. The FlexBot Powered OFF maintenance state should be used whenever possible.

Figure 44 - Port Side Panel with Power Switch in Vertical Off Position

2. E-Stop State - When engaged, the E-Stop will inhibit all motors. This includes both drive motors, lift motor, and rotation motor.

The E-Stop should be engaged before powering on the FlexBot and used for maintenance that requires power but no movement.

The E-Stop should be engaged when troubleshooting anything on the FlexBot other than the motors.

3. FlexBot in FlexBot Maintenance Cradle - Placing the FlexBot in the Maintenance Cradle creates a safe environment to give the FlexBot motor commands allowing the drive wheels to spin freely with no FlexBot horizontal motion.

Some maintenance processes require giving the FlexBot commands wirelessly through a computer. A maintenance dongle is required to be attached to the FlexBot so the computer can send and receive information to the FlexBot.

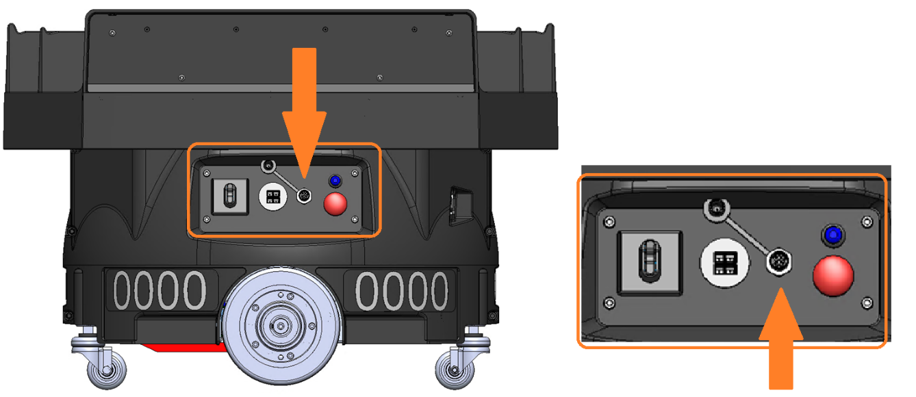
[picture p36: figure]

Figure 45 - Maintenance Dongle Receptable Location

Figure 46 - Before and after Maintenance Dongle attachment

After performing maintenance on the FlexBot, depending on the maintenance, a driving test is usually performed to ensure proper function of the FlexBot. The drive test is performed on the FlexField. Before running the test, the FlexBot should be placed on the field with barriers around it to stop it if there is a malfunction. The maintenance dongle is also used in this process.

# FlexBot Commissioning

When a FlexBot is received into a production environment from the manufacturer, a warehouse, or back from repair, it must be commissioned. The commissioning process is a step-by-step procedure for making sure that the FlexBot operates as it is supposed to.

This process makes sure that nothing happened to the FlexBot during storage or shipping. In the Index of Maintenance Procedures, all commissioning procedures are identified.

## Unboxing

The FlexBot is shipped in a reusable package. These packages should not be disposed of and should be kept in case the FlexBot needs to be shipped off site. During the unboxing process it is important to track serial numbers and license plate numbers for internal record keeping.

## General Functionality Testing

The general functionality testing puts the FlexBot through a battery of tests to make sure that all features of the FlexBot work properly. This test is broken into two parts, a static function test and a driving function test.

### FlexBot Static Function Test

This is the first test to make sure all components function properly. This evaluates the motors, the sensors, and makes sure all the wiring properly routed and connected. This test is performed on a maintenance cradle to ensure safe working conditions.

Use of the Maintenance Cradle allow testing of the FlexBot; keeping the wheels elevated to prevent movement across the floor or table. These tests can spin the drive wheels, raise, lower, and rotate the payload deck, and ensure all the associated sensors work while performing all these operations.

### FlexBot Drive Test

After the FlexBot passes the static function test it is considered safe to drive, but not safe to put into production. After performing and passing the Drive test it will be safe to put into production. The Drive test is a basic test putting the FlexBot through a basic list of normal operations it would see in production.

In this test the FlexBot will perform driving, rotating, shelving, picking up containers, dropping off containers, and other functions that it would see in a production environment. This test should be performed in a safe environment with barriers to keep people safe.

# FlexBot Preventive Maintenance

The FlexBot is a device that requires normal maintenance and inspections. It is recommended that these procedures are performed every 150 miles to ensure proper function. All preventative procedures are identified in the Maintenance Procedures Index.

## 150 Mile Inspection

The 150 Mile inspection is performed to make sure major components in the FlexBot are functioning properly and not showing any signs of major wear. The procedures and inspection points for the 150 Mile Inspection include:

- Deck Inspection and Cleaning
- Housing and License Plate Inspection
- Caster Inspection and Cleaning
- Port and Starboard Panel Inspection
- Cable Management Inspection
- PGV Inspection and Cleaning
- Deck Presence Sensor Inspection and Cleaning
- Drive Wheel Inspection and Cleaning

These are the major areas of wear in the FlexBot. If wear is noted during these inspections service or maintenance is recommended correcting noted discrepancies.

Other components of the FlexBot may also show wear that are not part of these inspections. If other aspects show excessive wear or damage they should also be serviced at this time.

# FB Maintenance Tool

The FB Maintenance Tool is a custom piece of software created by Berkshire Grey. This software is loaded on a RT laptop and is used by Robotics Technicians (RTs) to control a FlexBot for diagnostic, maintenance, and repair purposes when the FlexBot is off the FlexField.

Some commands in the FB Maintenance Tool are also used during FlexBot commissioning to verify the FlexBot is ready for service. The FB Maintenance Tool can command and control various key systems on the FlexBot once connected to a FlexBot under evaluation.

| When using the FB Maintenance tool, the maintenance dongle must be installed on the FlexBot. The FlexBot must be secured in the Maintenance Cradle for all tests except the Driving test. Do not use the FB Maintenance tool while the FlexBot is under full control of the orchestrator. For more information, see: - BG FlexBot 1010-01 FlexBot - FB Maintenance Tool on the RT Laptop - BG FlexBot 1002-01-Maintenance Dongle Use

## Files Needed on the RT Laptop

Before the FB Maintenance Tool can be used, these things must be true:

- The RT laptop is on the same Wi-Fi network as the FlexBot.
- The FlexBot IP address is known.
- These additional files are added to the RT laptop within the location of the tool files on the computer before the FB Maintenance Tool software is started:

bot file - This file controls various parameters of the FlexBot’s operations when using FB Maintenance tool.

map file - This file is a map of the fiducial location on the test field that certain tests will be executed on.

goal file - This file is the sequence of action that the FlexBot will perform for the driving test option of FB Maintenance Tool

Without these three files in place, FB Maintenance tool gives an error during the tool startup process.

Notice | The map and goal files must be presented on the system even when a drive test is not planned or used.

Once FB Maintenance tool is connected, it will download the relevant files onto the FlexBot and the terminal program on the computer will display a list of available commands. These commands are described in detail in the BG FlexBot 1010-01 FlexBot - FB Maintenance Tool on the RT Laptop document.

The FB Maintenance tool commands can be categorized into a few general groups:

- Individual drive and motion tests - Used to operate the various motors at specified speed and toggle motor brakes
- Sensor and readout tests - Used to test PGV, IMU, BMS, deck presence sensor, and the LED panel
- Comprehensive system tests such as the validation test and driving test
- Retrieve FlexBot logs such as telemetry, fb-robot stdout
- Deck encoder calibration - Note: This is the only sensor calibration available from FB Maintenance Tool
- Power off FlexBot and exit the program

Some individual system command and tests, such as the motor drive tests, will require user input or interaction such as specifying drive speed or LED color choices. These tests will often have limits to the range of inputs available to the user.

Other commands, such as for the PGV and IMU, will only display a reading or the result.

Commands like toggling the motor breaks will have no displayed output on the RT laptop.

Motor drive tests and sensor tests will remain active until the user exits out of the command using the appropriate command.

## Comprehensive Tests

The two comprehensive system tests in FB Maintenance are Validation test and Driving test.

The Validation test is a pre-programmed set of tests of the FlexBot onboard systems. It covers most, but not all, of the individual drive and motion test and sensor and readout tests.

The user input required for the Validation test is for the RT to verify whether the FlexBot successfully performed an action before moving onto the test action. All other characteristics are pre-set.

The Driving test is the only FB Maintenance tool test that requires the FlexBot to be position in a FlexField with fiducials.

Once entered, the Drive test will direct the FlexBot to follow the sequence of actions in the goal file loaded when FB Maintenance tool executed.

Upon the completion of the Drive test, FB Maintenance tool will automatically write the fb-robot stdout log file to the computer. The fb-robot stout log file can be found in the folder where the FB Maintenance tool files on the computer is kept. This file contains all relevant outputs and readouts from the FlexBot during the Drive test and may be used to help diagnose any issues.

Once all operations and testing are complete, the user can soft power off the FlexBot by using the Power off and exit command. This will set all FlexBot motor drive brakes and close any active connections the FlexBot has with any other systems as well as exit FB Maintenance tool. It’s important to note that this is not a safe power off state. All of the components still have electricity slowing to them.

However, the FlexBot is still partially on and drawing power. To fully power off the FlexBot, the user must physically turn the onboard power switch to the off (vertical) position. If the user wishes to reconnect to the FlexBot after the power off and exit command has been entered, the FlexBot must be physically power cycled.

# FlexBot Maintenance Procedures Index

Description | Subsystem | PM | CM | SAFETY | Commissioning | Document Number
FlexBot Unboxing Procedure | FlexBot | | | | ✓ | BG FlexBot 1001-01 FlexBot Unboxing Procedure
Maintenance Dongle Usage | FlexBot | ✓ | ✓ | ✓ | ✓ | BG FlexBot 1002-01-Maintenance Dongle Use
Belt Tension Diagnosis | Rotary Stage | ✓ | ✓ | | | BG FlexBot 1004-01 Deck Belt - Tension Inspection
Slip Ring and G-Clip Check | Rotary Stage | | ✓ | | | BG FlexBot 1007-01 Slip Ring & G-Clip - Check
Remove and Replace APB | Drive Base | | ✓ | | | BG FlexBot 1009-01 APB - Remove and Replace
Reset Button Replacement | Drive Base | | ✓ | | | BG FlexBot 1011-01 Reset Button Remove and Replace
Belt Replacement | Rotary Stage | | ✓ | | | BG FlexBot 1013-01 Belt - Remove and Replace
Bot Safety E-Stop Replacement | Drive Base | | ✓ | | | BG FlexBot 1014-01 Safety E-Stop - Remove and Replace
Cable Management Inspection | Drive Base | ✓ | ✓ | | | BG FlexBot 1015-01- Cable Management Inspection
Can Cable Replacement | Drive Base | | ✓ | | | BG FlexBot 1016-01 CAN Cable - Remove and Replace
Caster Plate Replacement | Drive Base | | ✓ | | | BG FlexBot 1018-01 Caster Plate - Remove and Replace
Deck Inspection and Cleaning | Payload Deck | ✓ | ✓ | | | BG FlexBot 1021-01 Deck Inspection and Cleaning
Drive MCB Replacement | Drive Base | | ✓ | | | BG FlexBot 1025-01 Drive MCB Remove and Replace
Drive Test | FlexBot | ✓ | ✓ | | ✓ | BG FlexBot 1026-01 Drive Test

Description | Subsystem | PM | CM | SAFETY | Commissioning | Document Number
FlexBot Packing Procedure | FlexBot | | ✓ | | | BG FlexBot 1030 -01 FlexBot - Return to Manufacturer
Full Commission Process | FlexBot | | | | ✓ | BG FlexBot 1032 -01 FlexBot - Full Commissioning
General Function Test | FlexBot | ✓ | ✓ | | ✓ | BG FlexBot 1033 -01 General Function Test
LCD Replacement | Drive Base | | ✓ | | | BG FlexBot 1034 -01 LCD - Remove and Replace
License Plate Replacement on Skin | FlexBot | | ✓ | | | BG FlexBot 1035 -01 - License Plate Remove and Replace
Lift MCB Replacement | Lift/Lower | | ✓ | | | BG FlexBot 1036 -01 Lift MCB - Remove and Replace
Lift Sensor Replacement | Lift/Lower | | ✓ | | | BG FlexBot 1037 -01 Lift Sensor - Remove and Replace
Network Antenna Replacement | Drive Base | | ✓ | | | BG FlexBot 1038 -01 Network Antenna - Remove and Replace
PDB Replacement | Drive Base | | ✓ | | | BG FlexBot 1039 -01 PDB - Remove and Replace
PGV Inspection and Cleaning | Drive Base | ✓ | ✓ | | | BG FlexBot 1041 -01 PGV - Cleaning
PGV Replacement | Drive Base | | ✓ | | | BG FlexBot 1042 -01 PGV - Remove and Replace
Plc Replacement | Drive Base | | ✓ | | | BG FlexBot 1043 -01 PLC - Remove and Replace
Deck Presence Sensor Inspection and Cleaning | Payload Deck | ✓ | ✓ | | | BG FlexBot 1045 -01 Deck Presence Sensors Inspect and Clean

Description | Subsystem | PM | CM | SAFETY | Commissioning | Document Number
Remove and Replace Drive Motor | Drive Base | | ✓ | | | BG FlexBot 1046 -01 Drive Motor - Remove and Replace
Remove and Replace Lift Motor | Lift/Lower | | ✓ | | | BG FlexBot 1047 -01 Lift Motor - Remove and Replace
Remove and Replace Lift Motor Linkage | Lift/Lower | | ✓ | | | BG FlexBot 1048 -01 Lift Motor Linkage - Remove and Replace
Remove and Replace Rotary Motor | Rotary Stage | | ✓ | | | BG FlexBot 1049 -01 Rotor Motor - Remove and Replace
Remove and Replace Slew Ring Assembly (Rotary Motor Assembly.) | Rotary Stage | | ✓ | | | BG FlexBot 1051-01 - Rotary Stage Assembly Remove and Replace
Shield Removal and Replacement | Rotary Stage | | ✓ | | | BG FlexBot 1056 -01 Shield - Remove and Replace
Terminal Block Replacement | Drive Base | | ✓ | | | BG FlexBot 1059 -01 - Terminal Block and Power Switch Remove and Replace
LED Replacement | Drive Base | | ✓ | | | BG FlexBot 1062 -01 LED - Remove and Replace
Charge Battery | Battery | ✓ | ✓ | | ✓ | BG FlexBot 1063 -01 Battery - Charging Procedure
Drive Wheel Shaft and Bearing Face Cleaning | Drive Base | ✓ | | | | BG FlexBot 1064 -01 Drive Wheel Cleaning and Inspection
Caster Inspection and Cleaning | Drive Base | ✓ | ✓ | | | BG FlexBot 1066 -01 - Caster Inspection and Cleaning
150 Mile FlexBot Inspection | FlexBot | ✓ | | | | BG FlexBot 1076-01- FlexBot 150 Mile Inspection
Battery Change Procedure | Battery | | ✓ | | | BG FlexBot 1077-01 Battery Change

Description | Subsystem | PM | CM | SAFETY | Commissioning | Document Number
Deck Presence Sensor Replacement | Payload Deck | | ✓ | | | BG FlexBot 1078-01- Deck Presence Sensor Replacement
How To Access Scissor Lift (Payload Deck Raise) | Lift/Lower | ✓ | ✓ | | ✓ | BG FlexBot 1079 -01 - Payload Deck Raise procedure
Maintenance States | FlexBot | | | ✓ | | BG FlexBot 1080 -01 - FlexBot Maintenance States
How To Use FRT | FlexBot | | | ✓ | | BG FlexBot 1081-01 - FlexBot Removal Tool Use Guide
FlexBot Maintenance Cradle | FlexBot | | | | | BG FlexBot 1082-01 - FlexBot Maintenance Cradle Use Guide
How To Team Lift FlexBot Safely | FlexBot | | | ✓ | | BG FlexBot 1083-01 - FlexBot Manual Team Lift
How To Use VRC Lift Safely | FlexBot | | | ✓ | | BG FlexBot 1084-01 - Vertical Reciprocating Conveyor Usage
Deck Replacement | Payload Deck | | ✓ | | | BG FlexBot 1086-01 - Payload Deck Replacement
Check Panel Connections | Drive Base | ✓ | ✓ | | | BG FlexBot 1087-01 - Panel Connections Inspection
ESD Procedure | FlexBot | | | ✓ | | BG FlexBot 1088-01 - Electro-Static Discharge Setup, Checks, and Use
Safe Battery Handling | Battery | | | ✓ | | BG FlexBot 1089-01 - Overview of Safe Battery Handling
Printing License Plate Procedure | FlexBot | | ✓ | | | BG FlexBot 1090-01 -License Plate -Printing
Inspect Housing and License Plate | Payload Deck | ✓ | ✓ | | | BG FlexBot 1091-01 - FlexBot Housing Inspection
FlexBot Belt Tensioning | FlexBot | | ✓ | | | BG FlexBot 1092-01 - Belt Tensioning
How To Inspect Scissor Lift | Lift/Lower | ✓ | ✓ | | | BG FlexBot 1093-01 - Scissor Lift Inspection
Scissor Lift Roller Channel Inspection | Lift/Lower | ✓ | ✓ | | | BG FlexBot 1094-01 - Scissor Lift Roller Channel Inspection
Lifter Arm Mount Wear Inspection | Lift/Lower | ✓ | ✓ | | | BG FlexBot 1095-01 - Lifter Arm Mount Wear Inspection
FlexBot Battery Revision and Serial Number Check | FlexBot | ✓ | ✓ | | ✓ | BG FlexBot 1097-01 - Battery Revision Check
Drive Motor Troubleshooting Process | Drive Base | | ✓ | | | BG FlexBot 1100-01 - Drive Motor Trouble Shooting Process
Rotate MCB Replacement | Rotary Stage | | ✓ | | | BG FlexBot 1101-01 - Rotate MCB Replacement
Replace G-Clip | Payload Deck | | ✓ | | | BG FlexBot 1102-01 - Replace G-Clip
Adding FlexBot to The FlexField | FlexBot | | | ✓ | | BG FlexField 3006-01-FlexBot Addition to FlexField
Removing FlexBot from The FlexField | FlexBot | | | ✓ | | BG FlexField 3007-01-FlexBot Removal from FlexField
LabelTac Printer Set Up | FlexBot | | ✓ | | | BG FlexField 3019-01-Printer Setup for Fiducials and License Plates

Business Sensitive - Not for Redistribution to Customer or Vendor Confidential & Proprietary © Berkshire Grey, Inc. 2022 Non-controlled copy in printed form. Check online system to ensure latest version. Page 56 of 57

FlexBot Manual

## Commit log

2026-04-03 Updated readme for network and lidar setup
2026-04-15 trying something new to cleanup udp communication and add battery info
2026-04-28 cleaned up some bringup bugs and setup state_estimation to just used wheel odometry for now
2026-05-11 updated readme and added CAD/documentation to repo
    [VLP16_mount.stl, computer_mount.stl, flir_camera_stand.stl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]
